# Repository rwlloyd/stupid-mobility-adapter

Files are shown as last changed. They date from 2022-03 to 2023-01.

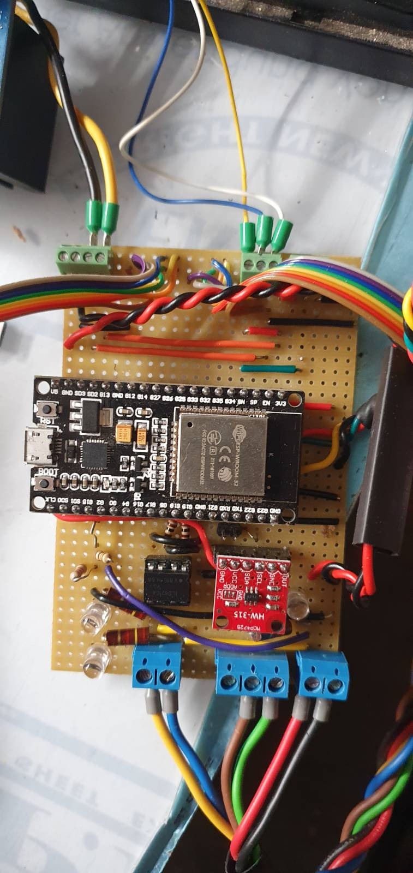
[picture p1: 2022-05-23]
signal-2022-04-29-131654.jpeg

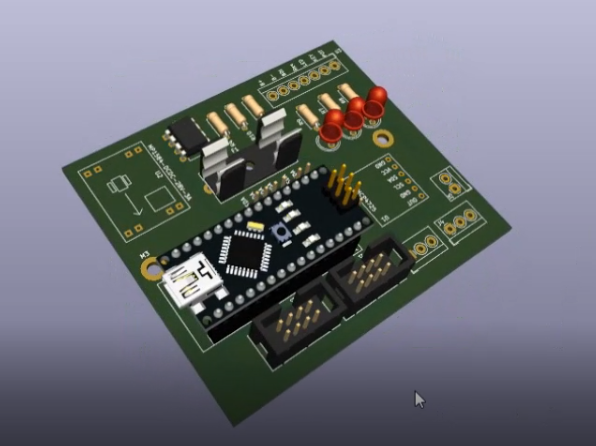
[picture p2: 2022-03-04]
stupid-mob-adap-v2-pcb-4-3-22.png

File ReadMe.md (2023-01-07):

# stupid-mobility-adapter

A repository for various microcontroller breakout boards that can be used to control mobile platforms (Modified Mobility Scooters).

## History of the stupid-mobility-adapter

During the COVID lockowns of 2020/21, it became necessary for me to have a Robotic platform that would work as a testing analogue to the one I didn't have access to at the time. This is how 'Scooterbot' was born. Initially intended as a personal, stipped back platform, liberated from the scrapheap, and built at minimal cost (<£250) the controller was fried and it had no steering column. These were replaced by an atmega 328 microcontroller and two BTS7960 half-bridge drivers. The PWM controlled drivers control the main DC drive motor and a steering motor. In this case, a 24V transaxle motor rated a 300-400W and a 24V linear actuator with feedback via a potentiometer (0-5V). Additionally, the drive motor has a 24V solenoid brake. 

After returning to work after lockdowns. A redesign of the platform I had been working on allowed me to use a modified version of the Scooterbot code to advance the project for work. This involved adding the ability to control a 'Curtis' style motor controller (Essentially three additional output signals. Enable, Direction and Speed (TTL, TTL, 0-5V)).

In addition to having a microcontroller to tell the motors, actuators etc. what to do. We also need to tell the microcontroller what to do. In previous projects, the communication with the microcontroller has been done over Serial connection with a simple communication protocol. With the microcontroller acting as a reciever, the sender was a companion computer (Raspberry Pi 3B+) reading inputs from a bluetooth games controller with custom python code. 

The addition of a companion computer adds a great deal of connectivity and processing power. Unfortunately, it also increases the complexity of the setup, and points of failure. Considering that basic control of the platform is a safety critical system, it is desirable to simplify the design. Additionally, as the prototypes of this project have performed on a variety of hardware, it is desirable to make this hardware intentionally generic, while keeping in mind its intended purpose.

The next version of the controller changed the microcontroller used to the ESP32. This allows us to cut out the companion computer for basic remote control using a bluetooth controller. There is also the addition of wifi, OTA updates using suitable sized compiled firmware and a large number of interface options. Overall simplification along the thinking of 'the best part is no part'. The drawback of this system is a reduction in CPU processing power.  

---

### stupid mobility adapter v2 

The culmination of the work on the ScooterBot and ARWAC v4 platforms. This board is intentionally generic. 
At the time of writing. It is not intended to fabricate this board. However, the PCB design is complete to the point of passing all Electrical Rules Checks

Important Hardware:

- Arduino Nano
- Adafruit MCP4725 12-bit DAC
- ILD615-2 Dual Optoisolator
- MP1584 DCDC Step Down (28V 3A)

Optional:

- 2 x BTS7960 Half-Bridge motor Drivers
- 2 x Electric Linear Actuator
- Mobility Scooter with Curtis style I/O

---

### stupid mobility adapter v3

As above, but ported to ESP32 with the addition of a Sony Dualshock3 Games contoller. Probably add some more bells and whistles too. 

Possibly:
- CAN Bus Tranciever
- encoder input
- Relays - Done!
- Status LEDS - Done on  the board. Headers for the panel?
- OLED for feedback/errors/messages - This may end up being done with a web interface

and that's just the hardware. Because we're using an esp32, we have the option for adding things like:

- Wifi
- A web interface/feedback
- ROS support (using micro-ROS)

## v3 PCB Problems

- The GND next to the VIN pin on the ESP32 Socket must be isolated
    - REASON: I misread the name when Making the footprint. It's actually CMD ( Something to do with the SPI Falsh chip. If you don't disconnect it, the ESP32 Can't Boot)
- LED 'D1' has the polarity reversed on the silkscreen.
- FB_0 has 5V and GND silkscreen swapped.
- 5V label on FB_0 and FB_1 should be 3V3
- The Board needs reverse polarity protection. Don't ask me how I know.
- A power LED on the 24V input would be useful.
- Should have broken out some power next to communicaton connections (Like I did with the relays)
- The Buzzer footprint needs to be correct. And connected to a pin capable of output :( 
- The Battery divider cannot be used while Wifi is enabled. Only discovered after install :(
    - Note: ADC2 pins cannot be used when Wi-Fi is used. So, if you’re using Wi-Fi and you’re having trouble getting the value from an ADC2 GPIO, you may consider using an ADC1 GPIO instead, that should solve your problem. from https://randomnerdtutorials.com/esp32-adc-analog-read-arduino-ide/

### Should have dones;
- A way to adjust the actuator endpoints on the board?
- A way to adjust the potential divider for the raw battery monitor. They're already talking about 48V!

However, we're running out of pins and It's probably time to embrace CAN bus, make the esp32 the 'master' node, then have nodes for the motor driver(s) ;), Actuators and any other custom bits. We should also start to be able to begin to use automotive devices....  

## Version 3.1 ideas

before I've even really finished the v3 hardware design, I've found things that I think it would be remiss of me to plan for. With 20/20 hindsight, some of these should have been included from the beginning.

### Servo PWM control From flight controllers

Control of the vehicle by more common means should be included. The first one that jumps to mind is the PWM contol that usually output by model radio recievers,
such as the ardupilot variety - that this hardware is eventually intendended to coexist alongside.

To implement this, we would need to 

- hand over control to the ardupilot system, taking commands from the autopilot in the form of throttle and steering inputs. 

- converting Servo signals to suitable outputs for the curtis unit / pwm driver / servo / hoverboardwheel / odrive combo that you need. 
https://www.benripley.com/diy/arduino/three-ways-to-read-a-pwm-signal-with-arduino/
https://lastminuteengineers.com/handling-esp32-gpio-interrupts-tutorial/

This would currently be controlled by the ps3 controller inputs, allowing the user to select different control methods while keeping the ablilty to contol the platform in case of emergencies or testing. 

### ESP acts as a radio control reciever 

### Servo Input to Flight Controllers

### Ros Input control

Here we are at a point where I need external input. HOw do people want to control all of this?

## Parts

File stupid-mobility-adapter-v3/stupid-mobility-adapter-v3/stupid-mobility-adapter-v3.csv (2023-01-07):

Source: | D:\dev\stupid-mobility-adapter\stupid-mobility-adapter-v3\stupid-mobility-adapter-v3\stupid-mobility-adapter-v3.kicad_sch
Date: | 05/12/2022 11:17:33
Tool: | Eeschema (6.0.2)
Generator: | C:\Program Files\KiCad\6.0\bin\scripting\plugins/bom_csv_grouped_by_value.py
Component Count: | 38
Individual Components:
Item | Qty | Reference(s) | Value | LibPart | Footprint | Datasheet | Field4
 |  | BZ1 | Buzzer | Device:Buzzer | stuipid-electronics-components:Buzzer_ABT-460-RC | ~
 |  | D1 | STAT | Device:LED | LED_THT:LED_D5.0mm | ~
 |  | D2 | REV | Device:LED | LED_THT:LED_D5.0mm | ~
 |  | D3 | KEY | Device:LED | LED_THT:LED_D5.0mm | ~
 |  | D4 | LED | Device:LED | LED_THT:LED_D5.0mm | ~
 |  | D5 | LED | Device:LED | LED_THT:LED_D5.0mm | ~
 |  | F1 | Fuse | Device:Fuse | Fuse:Fuse_Blade_ATO_directSolder | ~
 |  | J1 | BTS7968-0 | Connector_Generic:Conn_02x04_Odd_Even | Connector_IDC:IDC-Header_2x04_P2.54mm_Vertical | ~
 |  | J2 | Act0-FB | Connector_Generic:Conn_01x03 | TerminalBlock_4Ucon:TerminalBlock_4Ucon_1x03_P3.50mm_Horizontal | ~
 |  | J3 | BTS7968-1 | Connector_Generic:Conn_02x04_Odd_Even | Connector_IDC:IDC-Header_2x04_P2.54mm_Vertical | ~
 |  | J4 | Act1-FB | Connector_Generic:Conn_01x03 | TerminalBlock_4Ucon:TerminalBlock_4Ucon_1x03_P3.50mm_Horizontal | ~
 |  | J5 | ESTOP_INPUT | Connector_Generic:Conn_01x02 | TerminalBlock_4Ucon:TerminalBlock_4Ucon_1x02_P3.50mm_Horizontal | ~
 |  | J6 | UART | Connector_Generic:Conn_01x02 | Connector_PinHeader_2.54mm:PinHeader_1x02_P2.54mm_Vertical | ~
 |  | J7 | Relays | Connector_Generic:Conn_01x04 | Connector_PinHeader_2.54mm:PinHeader_1x04_P2.54mm_Vertical | ~
 |  | J8 | I2C | Connector_Generic:Conn_01x02 | Connector_PinHeader_2.54mm:PinHeader_1x02_P2.54mm_Vertical | ~
 |  | J9 | BATT_MON_SELECT | Connector_Generic:Conn_01x03 | Connector_PinHeader_2.54mm:PinHeader_1x03_P2.54mm_Vertical | ~
 |  | J10 | UART | Connector_Generic:Conn_01x02 | Connector_PinHeader_2.54mm:PinHeader_1x02_P2.54mm_Vertical | ~
 |  | Q1 | 2N3904 | Transistor_BJT:2N3904 | Package_TO_SOT_THT:TO-92_Inline | https://www.onsemi.com/pub/Collateral/2N3903-D.PDF
 |  | Q2 | 2N3904 | Transistor_BJT:2N3904 | Package_TO_SOT_THT:TO-92_Inline | https://www.onsemi.com/pub/Collateral/2N3903-D.PDF
 |  | R1 | R10K | Device:R | Resistor_THT:R_Axial_DIN0207_L6.3mm_D2.5mm_P7.62mm_Horizontal | ~
 |  | R2 | R1K5 | Device:R | Resistor_THT:R_Axial_DIN0207_L6.3mm_D2.5mm_P7.62mm_Horizontal | ~
 |  | R3 | R2K | Device:R | Resistor_THT:R_Axial_DIN0207_L6.3mm_D2.5mm_P7.62mm_Horizontal | ~
 |  | R4 | 100 | Device:R | Resistor_THT:R_Axial_DIN0207_L6.3mm_D2.5mm_P7.62mm_Horizontal | ~
 |  | R5 | R1K | Device:R | Resistor_THT:R_Axial_DIN0207_L6.3mm_D2.5mm_P7.62mm_Horizontal | ~
 |  | R6 | 100 | Device:R | Resistor_THT:R_Axial_DIN0207_L6.3mm_D2.5mm_P7.62mm_Horizontal | ~
 |  | R7 | 2k4 | Device:R | Resistor_THT:R_Axial_DIN0309_L9.0mm_D3.2mm_P12.70mm_Horizontal | ~
 |  | R8 | 2k4 | Device:R | Resistor_THT:R_Axial_DIN0309_L9.0mm_D3.2mm_P12.70mm_Horizontal | ~
 |  | R9 | 2k4 | Device:R | Resistor_THT:R_Axial_DIN0309_L9.0mm_D3.2mm_P12.70mm_Horizontal | ~
 |  | R10 | R1K | Device:R | Resistor_THT:R_Axial_DIN0207_L6.3mm_D2.5mm_P7.62mm_Horizontal | ~
 |  | R11 | R1K | Device:R | Resistor_THT:R_Axial_DIN0207_L6.3mm_D2.5mm_P7.62mm_Horizontal | ~
 |  | R12 | R1K | Device:R | Resistor_THT:R_Axial_DIN0207_L6.3mm_D2.5mm_P7.62mm_Horizontal | ~
 |  | R13 | R1K | Device:R | Resistor_THT:R_Axial_DIN0207_L6.3mm_D2.5mm_P7.62mm_Horizontal | ~
 |  | R14 | 100 | Device:R | Resistor_THT:R_Axial_DIN0207_L6.3mm_D2.5mm_P7.62mm_Horizontal | ~
 |  | U1 | MCP4725-Sparkfun | stupid-electronics-components-library:MCP4725-Sparkfun | stuipid-electronics-components:MPC4725-Sparkfun | https://www.sparkfun.com/products/12918
 |  | U2 | MP1584-DCDC-28V-3A | stupid-electronics-components-library:MP1584-DCDC-28V-3A | stuipid-electronics-components:MP1584 | https://www.monolithicpower.com/en/documentview/productdocument/index/version/2/document_type/Datasheet/lang/en/sku/MP1584EN-LF-Z/document_id/204
 |  | U3 | stupid-curtis-unit-basic | stupid-electronics-components-library:stupid-curtis-unit-basic | TerminalBlock_Phoenix:TerminalBlock_Phoenix_MKDS-3-7-5.08_1x07_P5.08mm_Horizontal
 |  | U4 | DUAL-OPTO | SparkFun-DiscreteSemi:DUAL-OPTOISOLATOR_SOIC8 | Package_DIP:DIP-8_W7.62mm | https://www.vishay.com/docs/83652/ild615.pdf | ILD615-2
 |  | U5 | ESP32DevKitV1 | stupid-electronics-components-library:ESP32DevKitV1 | stuipid-electronics-components:ESP32-DevKitV1
Collated Components:
Item | Qty | Reference(s) | Value | LibPart | Footprint | Datasheet | Field4
1 | 1 | BZ1 | Buzzer | Device:Buzzer | stuipid-electronics-components:Buzzer_ABT-460-RC | ~
2 | 1 | D1 | STAT | Device:LED | LED_THT:LED_D5.0mm | ~
3 | 1 | D2 | REV | Device:LED | LED_THT:LED_D5.0mm | ~
4 | 1 | D3 | KEY | Device:LED | LED_THT:LED_D5.0mm | ~
5 | 2 | D4, D5 | LED | Device:LED | LED_THT:LED_D5.0mm | ~
6 | 1 | F1 | Fuse | Device:Fuse | Fuse:Fuse_Blade_ATO_directSolder | ~
7 | 1 | J1 | BTS7968-0 | Connector_Generic:Conn_02x04_Odd_Even | Connector_IDC:IDC-Header_2x04_P2.54mm_Vertical | ~
8 | 1 | J2 | Act0-FB | Connector_Generic:Conn_01x03 | TerminalBlock_4Ucon:TerminalBlock_4Ucon_1x03_P3.50mm_Horizontal | ~
9 | 1 | J3 | BTS7968-1 | Connector_Generic:Conn_02x04_Odd_Even | Connector_IDC:IDC-Header_2x04_P2.54mm_Vertical | ~
10 | 1 | J4 | Act1-FB | Connector_Generic:Conn_01x03 | TerminalBlock_4Ucon:TerminalBlock_4Ucon_1x03_P3.50mm_Horizontal | ~
11 | 1 | J5 | ESTOP_INPUT | Connector_Generic:Conn_01x02 | TerminalBlock_4Ucon:TerminalBlock_4Ucon_1x02_P3.50mm_Horizontal | ~
12 | 2 | J6, J10 | UART | Connector_Generic:Conn_01x02 | Connector_PinHeader_2.54mm:PinHeader_1x02_P2.54mm_Vertical | ~
13 | 1 | J7 | Relays | Connector_Generic:Conn_01x04 | Connector_PinHeader_2.54mm:PinHeader_1x04_P2.54mm_Vertical | ~
14 | 1 | J8 | I2C | Connector_Generic:Conn_01x02 | Connector_PinHeader_2.54mm:PinHeader_1x02_P2.54mm_Vertical | ~
15 | 1 | J9 | BATT_MON_SELECT | Connector_Generic:Conn_01x03 | Connector_PinHeader_2.54mm:PinHeader_1x03_P2.54mm_Vertical | ~
16 | 2 | Q1, Q2 | 2N3904 | Transistor_BJT:2N3904 | Package_TO_SOT_THT:TO-92_Inline | https://www.onsemi.com/pub/Collateral/2N3903-D.PDF
17 | 1 | R1 | R10K | Device:R | Resistor_THT:R_Axial_DIN0207_L6.3mm_D2.5mm_P7.62mm_Horizontal | ~
18 | 1 | R2 | R1K5 | Device:R | Resistor_THT:R_Axial_DIN0207_L6.3mm_D2.5mm_P7.62mm_Horizontal | ~
19 | 1 | R3 | R2K | Device:R | Resistor_THT:R_Axial_DIN0207_L6.3mm_D2.5mm_P7.62mm_Horizontal | ~
20 | 3 | R4, R6, R14 | 100 | Device:R | Resistor_THT:R_Axial_DIN0207_L6.3mm_D2.5mm_P7.62mm_Horizontal | ~
21 | 5 | R5, R10, R11, R12, R13 | R1K | Device:R | Resistor_THT:R_Axial_DIN0207_L6.3mm_D2.5mm_P7.62mm_Horizontal | ~
22 | 3 | R7, R8, R9 | 2k4 | Device:R | Resistor_THT:R_Axial_DIN0309_L9.0mm_D3.2mm_P12.70mm_Horizontal | ~
23 | 1 | U1 | MCP4725-Sparkfun | stupid-electronics-components-library:MCP4725-Sparkfun | stuipid-electronics-components:MPC4725-Sparkfun | https://www.sparkfun.com/products/12918
24 | 1 | U2 | MP1584-DCDC-28V-3A | stupid-electronics-components-library:MP1584-DCDC-28V-3A | stuipid-electronics-components:MP1584 | https://www.monolithicpower.com/en/documentview/productdocument/index/version/2/document_type/Datasheet/lang/en/sku/MP1584EN-LF-Z/document_id/204
25 | 1 | U3 | stupid-curtis-unit-basic | stupid-electronics-components-library:stupid-curtis-unit-basic | TerminalBlock_Phoenix:TerminalBlock_Phoenix_MKDS-3-7-5.08_1x07_P5.08mm_Horizontal
26 | 1 | U4 | DUAL-OPTO | SparkFun-DiscreteSemi:DUAL-OPTOISOLATOR_SOIC8 | Package_DIP:DIP-8_W7.62mm | https://www.vishay.com/docs/83652/ild615.pdf | ILD615-2
27 | 1 | U5 | ESP32DevKitV1 | stupid-electronics-components-library:ESP32DevKitV1 | stuipid-electronics-components:ESP32-DevKitV1

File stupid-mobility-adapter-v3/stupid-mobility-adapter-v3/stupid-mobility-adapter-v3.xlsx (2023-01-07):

Source: | D:\dev\stupid-mobility-adapter\stupid-mobility-adapter-v3\stupid-mobility-adapter-v3\stupid-mobility-adapter-v3.kicad_sch
Date: | 2022-11-21T21:58:15.99999999627470925
Tool: | Eeschema (6.0.0)
Generator: | C:\Program Files\KiCad\6.0\bin\scripting\plugins/bom_csv_grouped_by_value_with_fp.py
Component Count: | 38
Ref | Qnty | Value | Cmp name | Footprint | Description | Vendor
BZ1, | 1 | Buzzer | Buzzer | stuipid-electronics-components:Buzzer_ABT-460-RC | Buzzer, polarized
D1, | 1 | STAT | LED | LED_THT:LED_D5.0mm | Light emitting diode
D2, | 1 | REV | LED | LED_THT:LED_D5.0mm | Light emitting diode
D3, | 1 | KEY | LED | LED_THT:LED_D5.0mm | Light emitting diode
D4, D5, | 2 | LED | LED | LED_THT:LED_D5.0mm | Light emitting diode
F1, | 1 | Fuse | Fuse | Fuse:Fuse_Blade_ATO_directSolder | Fuse
J1, | 1 | BTS7968-0 | Conn_02x04_Odd_Even | Connector_IDC:IDC-Header_2x04_P2.54mm_Vertical | Generic connector, double row, 02x04, odd/even pin numbering scheme (row 1 odd numbers, row 2 even numbers), script generated (kicad-library-utils/schlib/autogen/connector/)
J2, | 1 | Act0-FB | Conn_01x03 | TerminalBlock_4Ucon:TerminalBlock_4Ucon_1x03_P3.50mm_Horizontal | Generic connector, single row, 01x03, script generated (kicad-library-utils/schlib/autogen/connector/)
J3, | 1 | BTS7968-1 | Conn_02x04_Odd_Even | Connector_IDC:IDC-Header_2x04_P2.54mm_Vertical | Generic connector, double row, 02x04, odd/even pin numbering scheme (row 1 odd numbers, row 2 even numbers), script generated (kicad-library-utils/schlib/autogen/connector/)
J4, | 1 | Act1-FB | Conn_01x03 | TerminalBlock_4Ucon:TerminalBlock_4Ucon_1x03_P3.50mm_Horizontal | Generic connector, single row, 01x03, script generated (kicad-library-utils/schlib/autogen/connector/)
J5, | 1 | ESTOP_INPUT | Conn_01x02 | TerminalBlock_4Ucon:TerminalBlock_4Ucon_1x02_P3.50mm_Horizontal | Generic connector, single row, 01x02, script generated (kicad-library-utils/schlib/autogen/connector/)
J6, J10, | 2 | UART | Conn_01x02 | Connector_PinHeader_2.54mm:PinHeader_1x02_P2.54mm_Vertical | Generic connector, single row, 01x02, script generated (kicad-library-utils/schlib/autogen/connector/)
J7, | 1 | Relays | Conn_01x04 | Connector_PinHeader_2.54mm:PinHeader_1x04_P2.54mm_Vertical | Generic connector, single row, 01x04, script generated (kicad-library-utils/schlib/autogen/connector/)
J8, | 1 | I2C | Conn_01x02 | Connector_PinHeader_2.54mm:PinHeader_1x02_P2.54mm_Vertical | Generic connector, single row, 01x02, script generated (kicad-library-utils/schlib/autogen/connector/)
J9, | 1 | BATT_MON_SELECT | Conn_01x03 | Connector_PinHeader_2.54mm:PinHeader_1x03_P2.54mm_Vertical | Generic connector, single row, 01x03, script generated (kicad-library-utils/schlib/autogen/connector/)
Q1, Q2, | 2 | 2N3904 | 2N3904 | Package_TO_SOT_THT:TO-92_Inline | 0.2A Ic, 40V Vce, Small Signal NPN Transistor, TO-92
R1, | 1 | R10K | R | Resistor_THT:R_Axial_DIN0207_L6.3mm_D2.5mm_P7.62mm_Horizontal | Resistor
R2, | 1 | R1K5 | R | Resistor_THT:R_Axial_DIN0207_L6.3mm_D2.5mm_P7.62mm_Horizontal | Resistor
R3, | 1 | R2K | R | Resistor_THT:R_Axial_DIN0207_L6.3mm_D2.5mm_P7.62mm_Horizontal | Resistor
R4, R6, R14, | 3 | 100 | R | Resistor_THT:R_Axial_DIN0207_L6.3mm_D2.5mm_P7.62mm_Horizontal | Resistor
R5, R10, R11, R12, R13, | 5 | R1K | R | Resistor_THT:R_Axial_DIN0207_L6.3mm_D2.5mm_P7.62mm_Horizontal | Resistor
R7, R8, R9, | 3 | 2k4 | R | Resistor_THT:R_Axial_DIN0309_L9.0mm_D3.2mm_P12.70mm_Horizontal | Resistor
U1, | 1 | MCP4725-Sparkfun | MCP4725-Sparkfun | stuipid-electronics-components:MPC4725-Sparkfun | Sparkfun 12-bit DAC- I2C
U2, | 1 | MP1584-DCDC-28V-3A | MP1584-DCDC-28V-3A | stuipid-electronics-components:MP1584
U3, | 1 | stupid-curtis-unit-basic | stupid-curtis-unit-basic | TerminalBlock_Phoenix:TerminalBlock_Phoenix_MKDS-3-7-5.08_1x07_P5.08mm_Horizontal
U4, | 1 | DUAL-OPTO | DUAL-OPTOISOLATOR_SOIC8 | Package_DIP:DIP-8_W7.62mm
U5, | 1 | ESP32DevKitV1 | ESP32DevKitV1 | stuipid-electronics-components:ESP32-DevKitV1 | kicad6.0 symbol for ESP32DevKitV1 Board

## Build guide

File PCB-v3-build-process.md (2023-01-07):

# Mobility Adapter PCB (v3) firmware configuration procedure

This configuration process guides you through preparing hardware and configuring firmware for the Mobility-Adapter-v3 PCB as of late 2022.  

## Cut redundant traces on PCB (v3).

The pin next to VIN on the ESP32 Module footprint, Labelled GND, is a mistake. The pis should not be connected to ground. 
1. Cut the traces for that pin, connecting it to the ground plane.

2. Check that the pin is isolated using a multimeter between the isolated pin and any other GND point.

## Adjust the Buck Converter Voltage

Once the main motor driver header, fuse and buck module are soldered, the output of the buck can be set to 5v.

1. Connect the 12-30v supply voltage to the B+ and B-. NOTE. This board doesn't have reverse polarity protection. DOUBLE CHECK POLARITY.

2. Power up the board and adjust the trim pot on the buck converter to 5.0 - 5.1V. The 5V and GNC pins associated with the relays header are convenient test points.

## Setup Bluetooth Controller 

1. Flash the Ps3Address.ino file to the ESP32. it can be found at;

`firmware\PS3Controller\Ps3Address\Ps3Address.ino`

2. install and run the 'SixAxisPairTool' and enter the MAC address discovered in the previous step.

3. test the pairing using the Ps3Test-Friendly.ino sketch, found at;

`firmware\PS3Controller\Ps3Test-Friendly\Ps3Test-Friendly.ino`

It's necessary to modify the folloing line in the setup function, substituting in the correct mac address for this particular pairing.

`Ps3.begin("xx:xx:xx:xx:xx:xx");`

## Configure Firmware for Specific Platform

While Each platform will need a custom configuration regarding the use of the output, all platforms will require the following modifications.

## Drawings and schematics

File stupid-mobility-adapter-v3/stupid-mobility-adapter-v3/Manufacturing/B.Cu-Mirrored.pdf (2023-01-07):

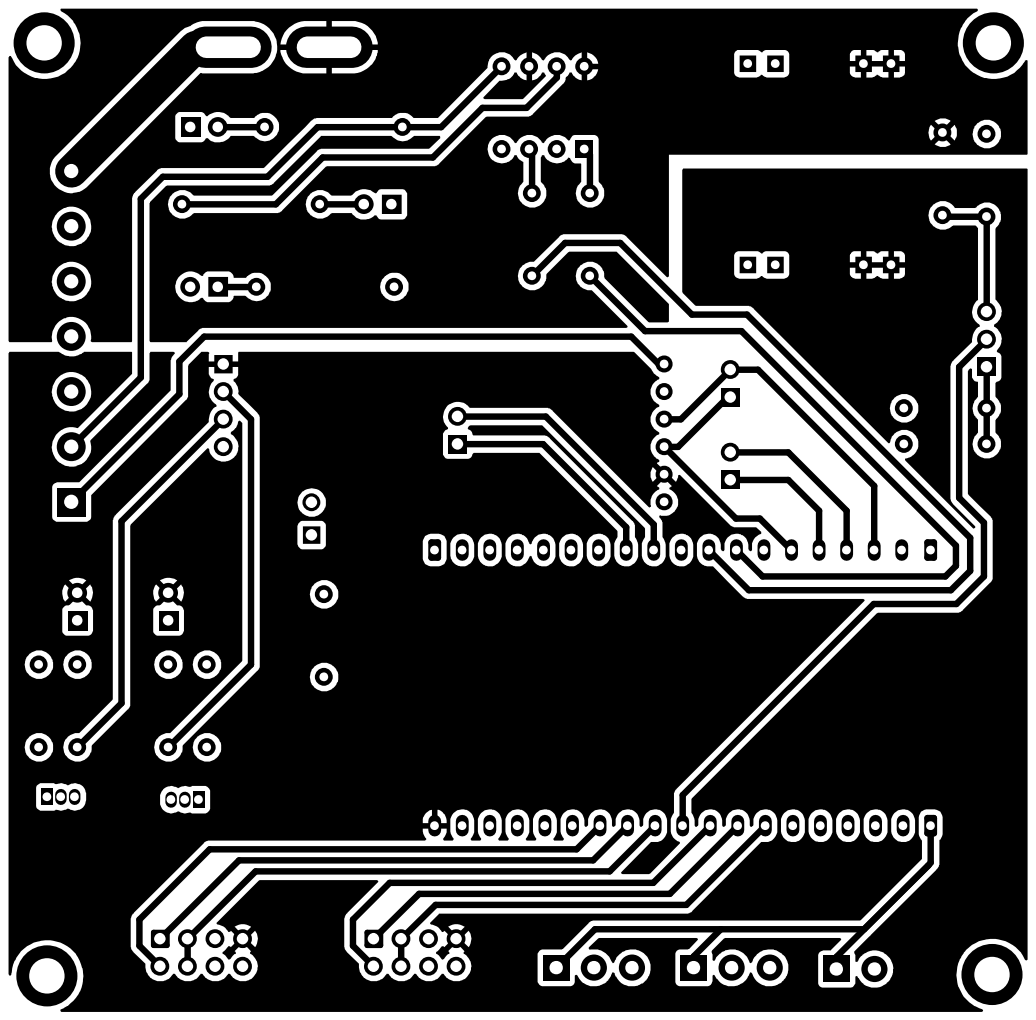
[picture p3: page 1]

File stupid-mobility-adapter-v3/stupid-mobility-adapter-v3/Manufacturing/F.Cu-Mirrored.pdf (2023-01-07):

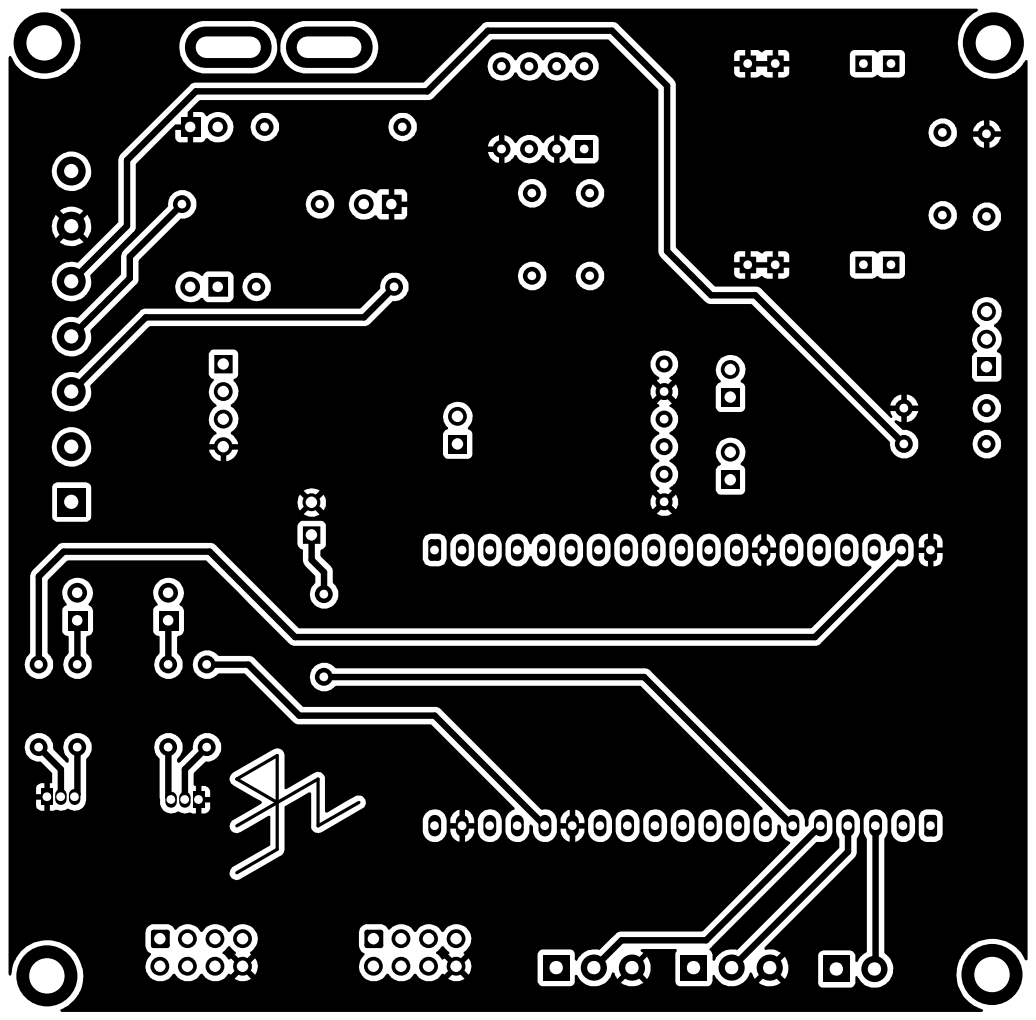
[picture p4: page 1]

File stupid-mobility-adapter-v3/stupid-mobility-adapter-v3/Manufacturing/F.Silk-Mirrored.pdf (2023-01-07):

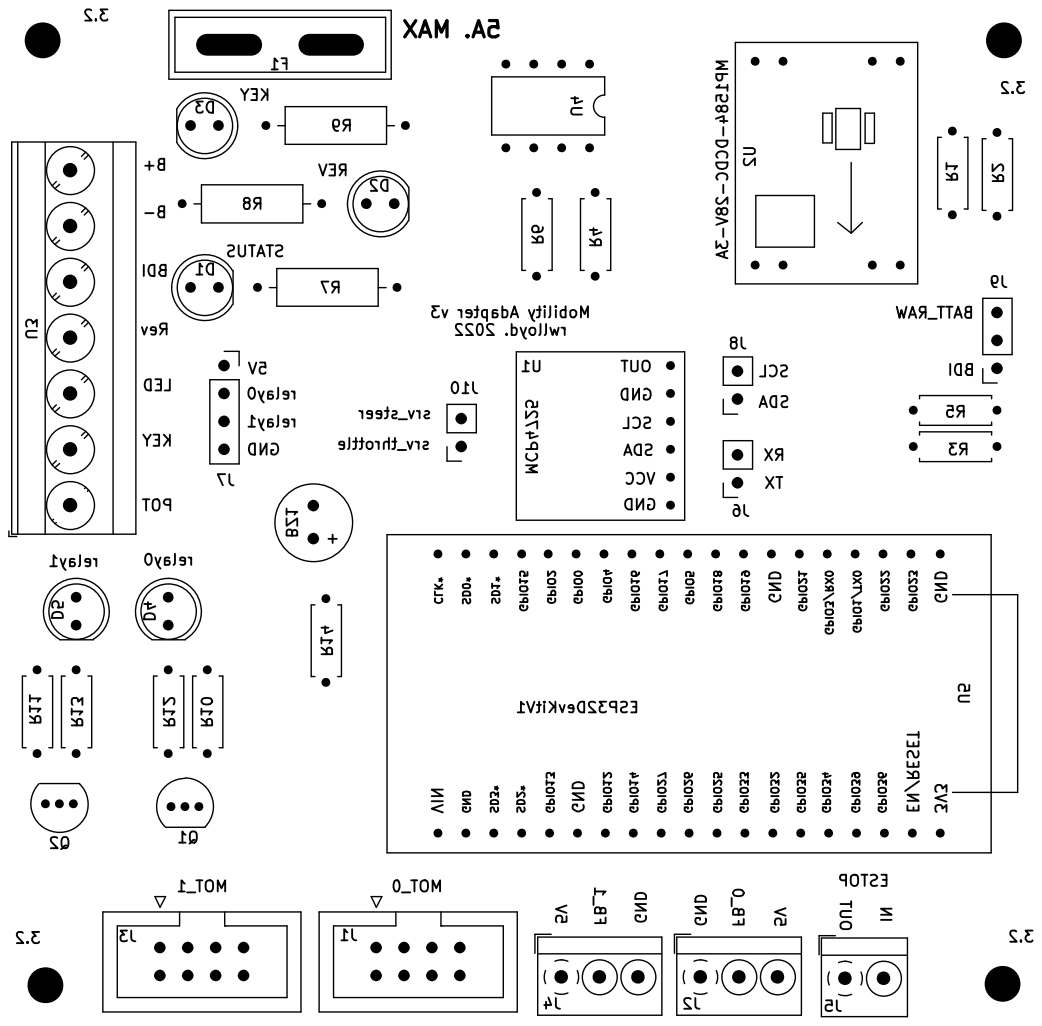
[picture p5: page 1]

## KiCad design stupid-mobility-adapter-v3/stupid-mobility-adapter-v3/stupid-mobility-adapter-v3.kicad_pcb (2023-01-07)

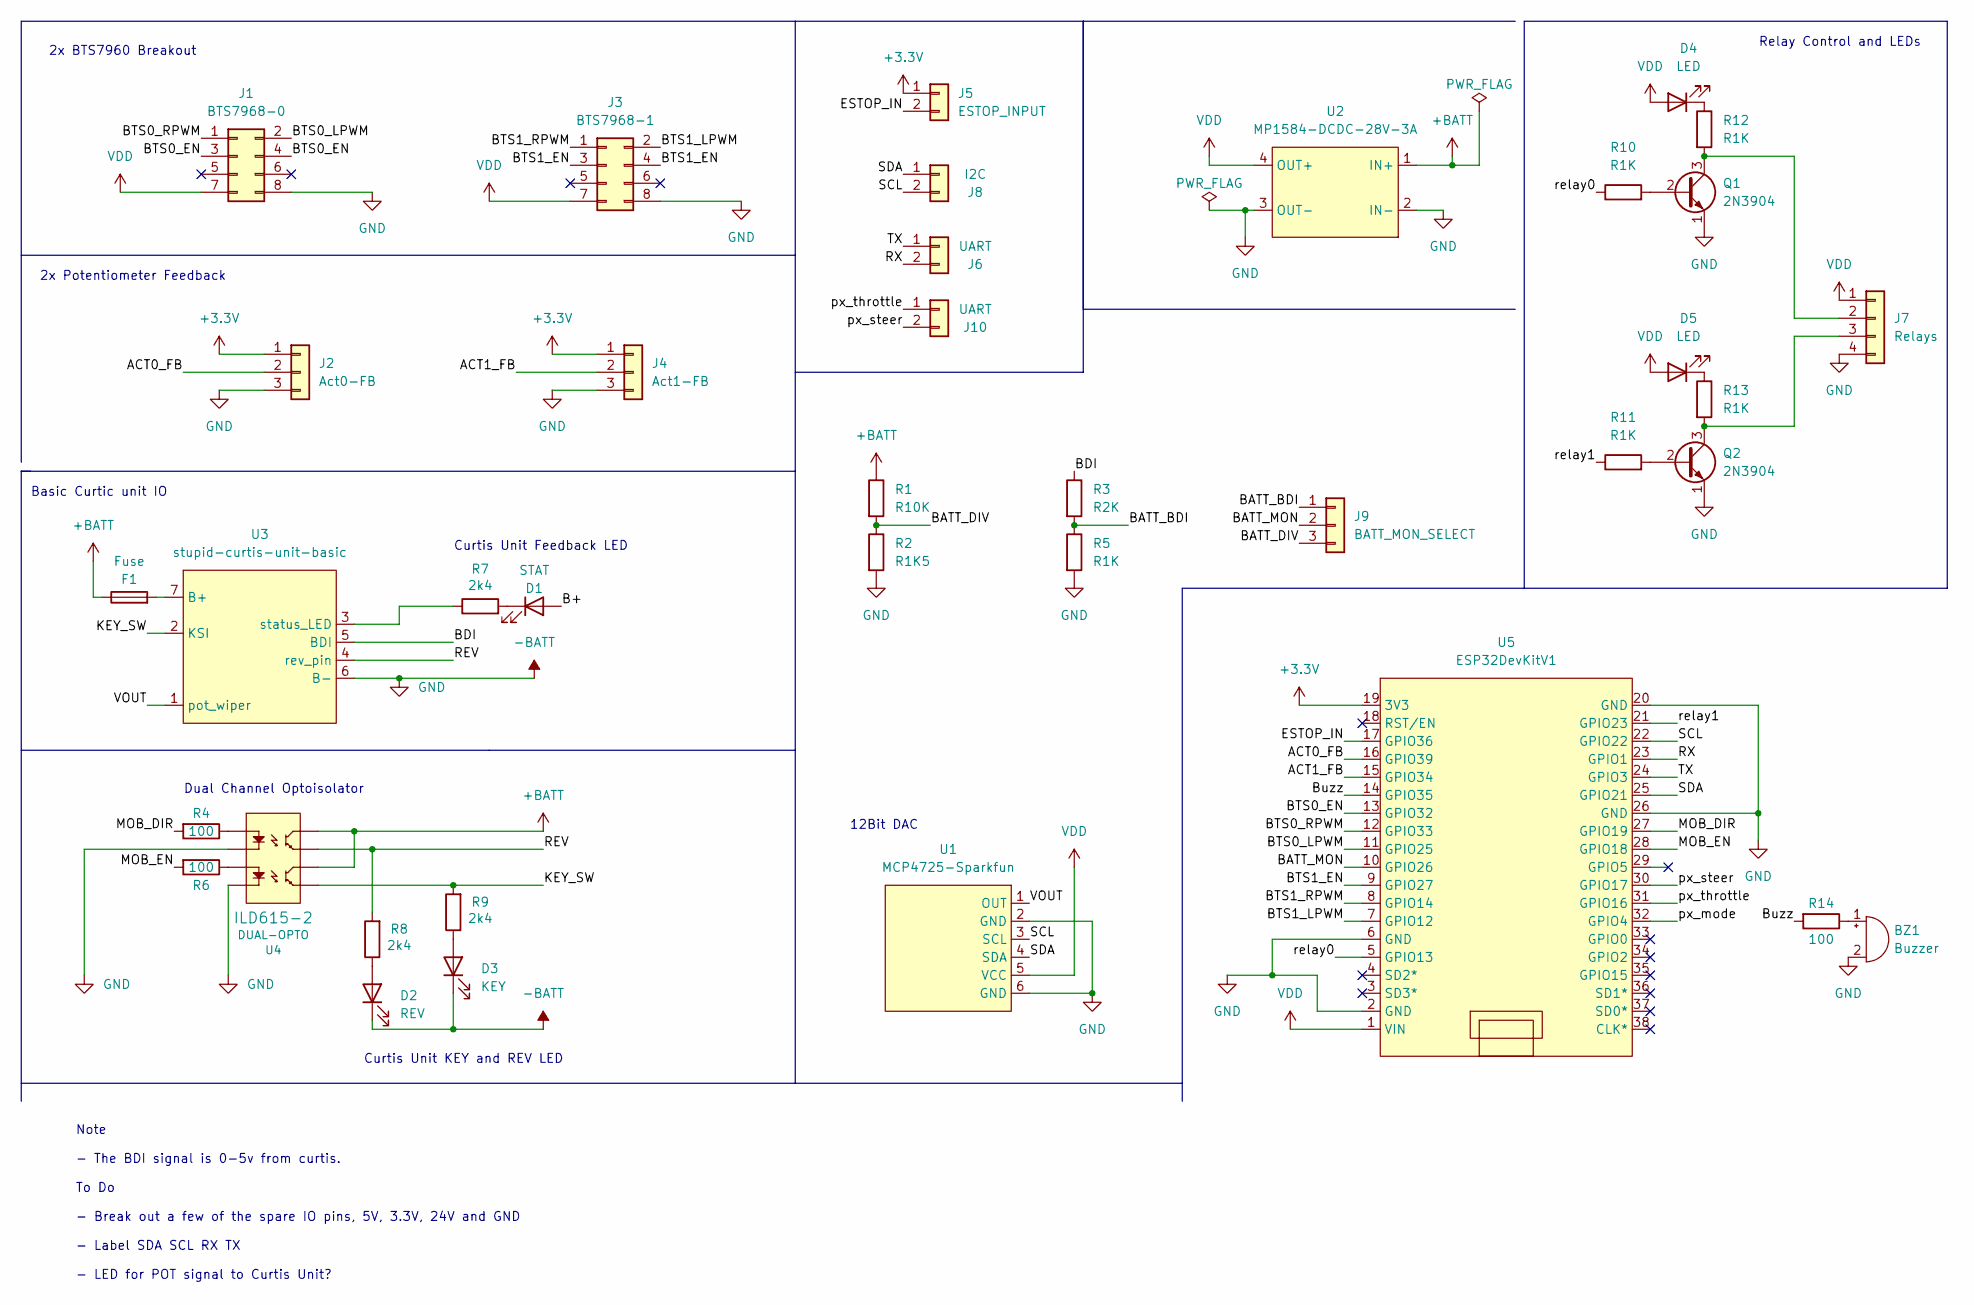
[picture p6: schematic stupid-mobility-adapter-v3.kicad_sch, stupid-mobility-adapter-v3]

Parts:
BZ1: Buzzer; Buzzer_ABT-460-RC
D1: STAT; LED_D5.0mm
D2: REV; LED_D5.0mm
D3: KEY; LED_D5.0mm
D4, D5: LED; LED_D5.0mm
F1: Fuse; Fuse_Blade_ATO_directSolder
J1: BTS7968-0; IDC-Header_2x04_P2.54mm_Vertical
J2: Act0-FB; TerminalBlock_4Ucon_1x03_P3.50mm_Horizontal
J3: BTS7968-1; IDC-Header_2x04_P2.54mm_Vertical
J4: Act1-FB; TerminalBlock_4Ucon_1x03_P3.50mm_Horizontal
J5: ESTOP_INPUT; TerminalBlock_4Ucon_1x02_P3.50mm_Horizontal
J6, J10: UART; PinHeader_1x02_P2.54mm_Vertical
J7: Relays; PinHeader_1x04_P2.54mm_Vertical
J8: I2C; PinHeader_1x02_P2.54mm_Vertical
J9: BATT_MON_SELECT; PinHeader_1x03_P2.54mm_Vertical
Q1, Q2: 2N3904; TO-92_Inline
R1: R10K; R_Axial_DIN0207_L6.3mm_D2.5mm_P7.62mm_Horizontal
R2: R1K5; R_Axial_DIN0207_L6.3mm_D2.5mm_P7.62mm_Horizontal
R3: R2K; R_Axial_DIN0207_L6.3mm_D2.5mm_P7.62mm_Horizontal
R4, R6, R14: 100; R_Axial_DIN0207_L6.3mm_D2.5mm_P7.62mm_Horizontal
R5, R10, R11, R12, R13: R1K; R_Axial_DIN0207_L6.3mm_D2.5mm_P7.62mm_Horizontal
R7, R8, R9: 2k4; R_Axial_DIN0309_L9.0mm_D3.2mm_P12.70mm_Horizontal
U1: MCP4725-Sparkfun; MPC4725-Sparkfun
U2: MP1584-DCDC-28V-3A; MP1584
U3: stupid-curtis-unit-basic; TerminalBlock_Phoenix_MKDS-3-7-5.08_1x07_P5.08mm_Horizontal
U4: DUAL-OPTO; DIP-8_W7.62mm
U5: ESP32DevKitV1; ESP32-DevKitV1

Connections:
+3V3: J2.1, J4.1, J5.1, U5.19 (3V3)
+BATT: F1.1, R1.1, U2.1 (IN+), U4.6 (CL2), U4.8 (CL1)
-BATT: BZ1.2 (+), D2.1 (K), D3.1 (K), J1.8, J2.3, J3.8, J4.3, J7.4, Q1.1 (E), Q2.1 (E), R2.2, R5.2, U1.2 (GND), U1.6 (GND), U2.2 (IN-), U2.3 (OUT-), U3.6 (B-), U4.2 (C1), U4.4 (C2), U5.2 (GND), U5.6 (GND), U5.20 (GND), U5.26 (GND)
/ACT0_FB: J2.2, U5.16 (GPIO39)
/ACT1_FB: J4.2, U5.15 (GPIO34)
/B+: D1.2 (A)
/BATT_BDI: J9.1, R3.2, R5.1
/BATT_DIV: J9.3, R1.2, R2.1
/BATT_MON: J9.2, U5.10 (GPIO26)
/BDI: R3.1, U3.5 (BDI)
/BTS0_EN: J1.3, J1.4, U5.13 (GPIO32)
/BTS0_LPWM: J1.2, U5.11 (GPIO25)
/BTS0_RPWM: J1.1, U5.12 (GPIO33)
/BTS1_EN: J3.3, J3.4, U5.9 (GPIO27)
/BTS1_LPWM: J3.2, U5.7 (GPIO12)
/BTS1_RPWM: J3.1, U5.8 (GPIO14)
/Buzz: R14.2, U5.14 (GPIO35)
/ESTOP_IN: J5.2, U5.17 (GPIO36)
/KEY_SW: R9.2, U3.2 (KSI), U4.5 (EM2)
/MOB_DIR: R4.2, U5.27 (GPIO19)
/MOB_EN: R6.2, U5.28 (GPIO18)
/REV: R8.2, U3.4 (rev_pin), U4.7 (EM1)
/RX: J6.2, U5.23 (GPIO1)
/SCL: J8.2, U1.3 (SCL), U5.22 (GPIO22)
/SDA: J8.1, U1.4 (SDA), U5.25 (GPIO21)
/TX: J6.1, U5.24 (GPIO3)
/VOUT: U1.1 (OUT), U3.1 (pot_wiper)
/px_mode: U5.32 (GPIO4)
/px_steer: J10.2, U5.30 (GPIO17)
/px_throttle: J10.1, U5.31 (GPIO16)
/relay0: R10.1, U5.5 (GPIO13)
/relay1: R11.1, U5.21 (GPIO23)
unnamed: BZ1.1 (-), R14.1
unnamed: D1.1 (K), R7.2
unnamed: D2.2 (A), R8.1
unnamed: D3.2 (A), R9.1
unnamed: D4.1 (K), R12.1
unnamed: D5.1 (K), R13.1
unnamed: F1.2, U3.7 (B+)
unnamed: J7.2, Q1.3 (C), R12.2
unnamed: J7.3, Q2.3 (C), R13.2
unnamed: Q1.2 (B), R10.2
unnamed: Q2.2 (B), R11.2
unnamed: R4.1, U4.1 (A1)
unnamed: R6.1, U4.3 (A2)
unnamed: R7.1, U3.3 (status_LED)
VDD: D4.2 (A), D5.2 (A), J1.7, J3.7, J7.1, U1.5 (VCC), U2.4 (OUT+), U5.1 (VIN)

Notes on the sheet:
2x BTS7960 Breakout
Basic Curtic unit IO
Curtis Unit KEY and REV LED
Dual Channel Optoisolator
12Bit DAC
Curtis Unit Feedback LED
Note - The BDI signal is 0-5v from curtis. To Do - Break out a few of the spare IO pins, 5V, 3.3V, 24V and GND - Label SDA SCL RX TX - LED for POT signal to Curtis Unit?
Relay Control and LEDs
2x Potentiometer Feedback

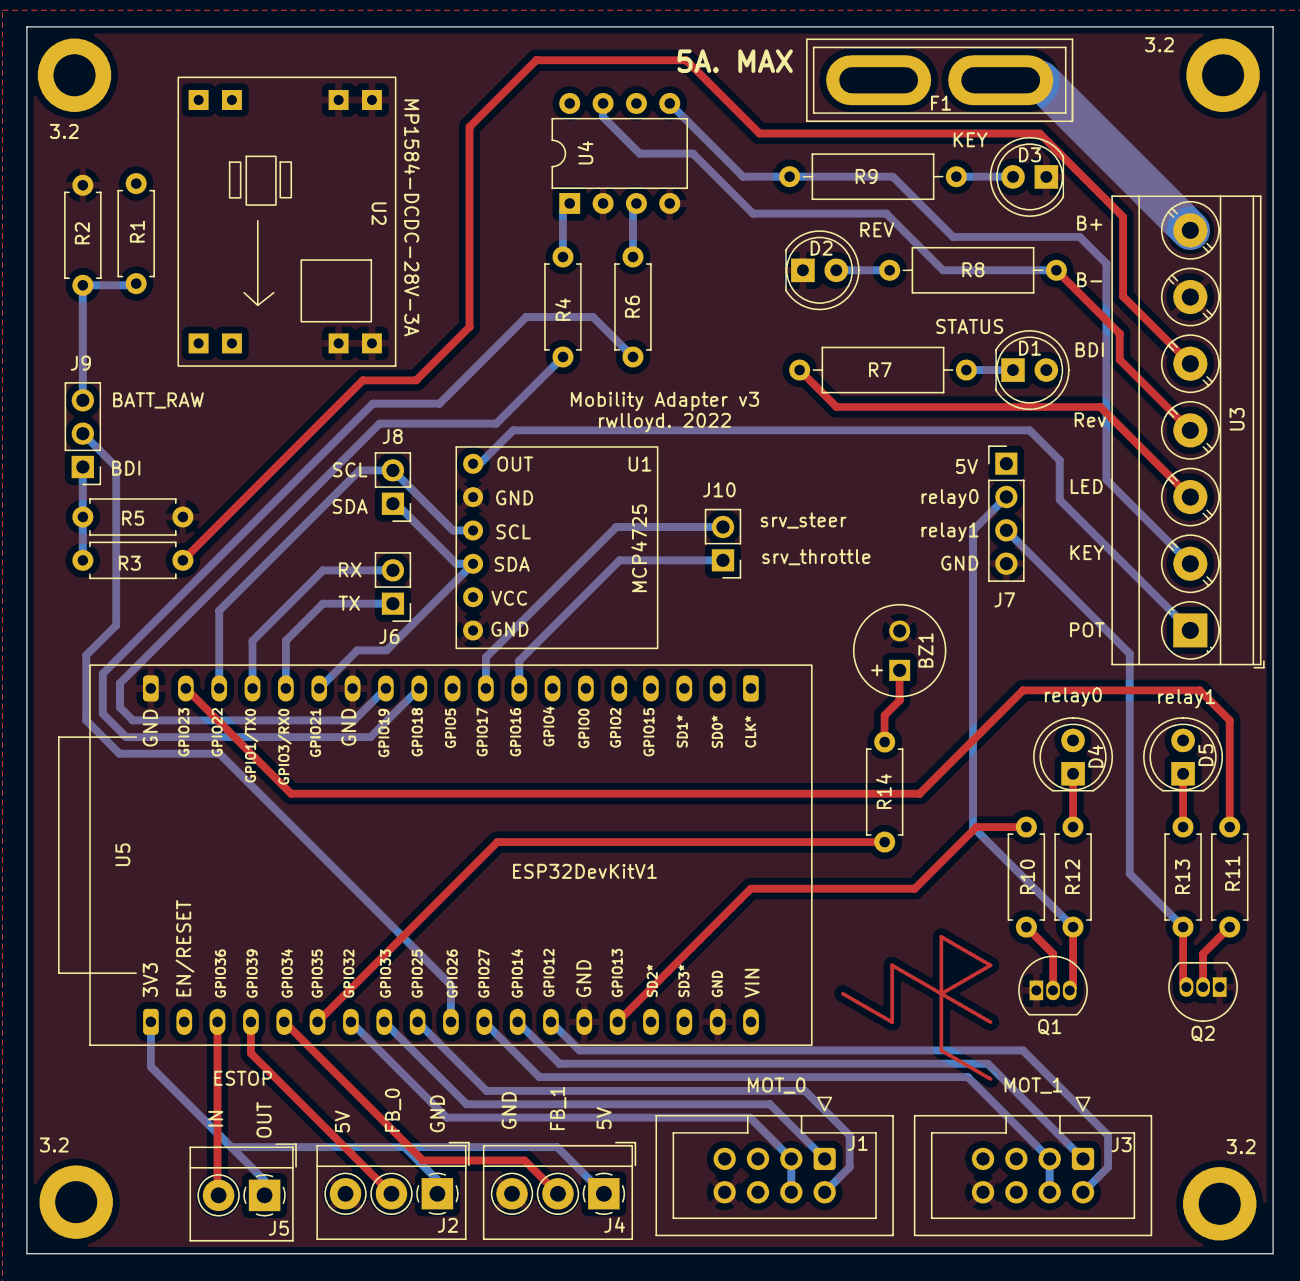
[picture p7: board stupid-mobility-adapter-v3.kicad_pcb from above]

Board: 2 copper layers, 94.9 x 93.5 mm, 42 parts (0 on the bottom side), 45 nets.

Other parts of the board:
3.2, 3.2#2, 3.2#3, 3.2#4: MountingHole_3.2mm_M3_DIN965_Pad

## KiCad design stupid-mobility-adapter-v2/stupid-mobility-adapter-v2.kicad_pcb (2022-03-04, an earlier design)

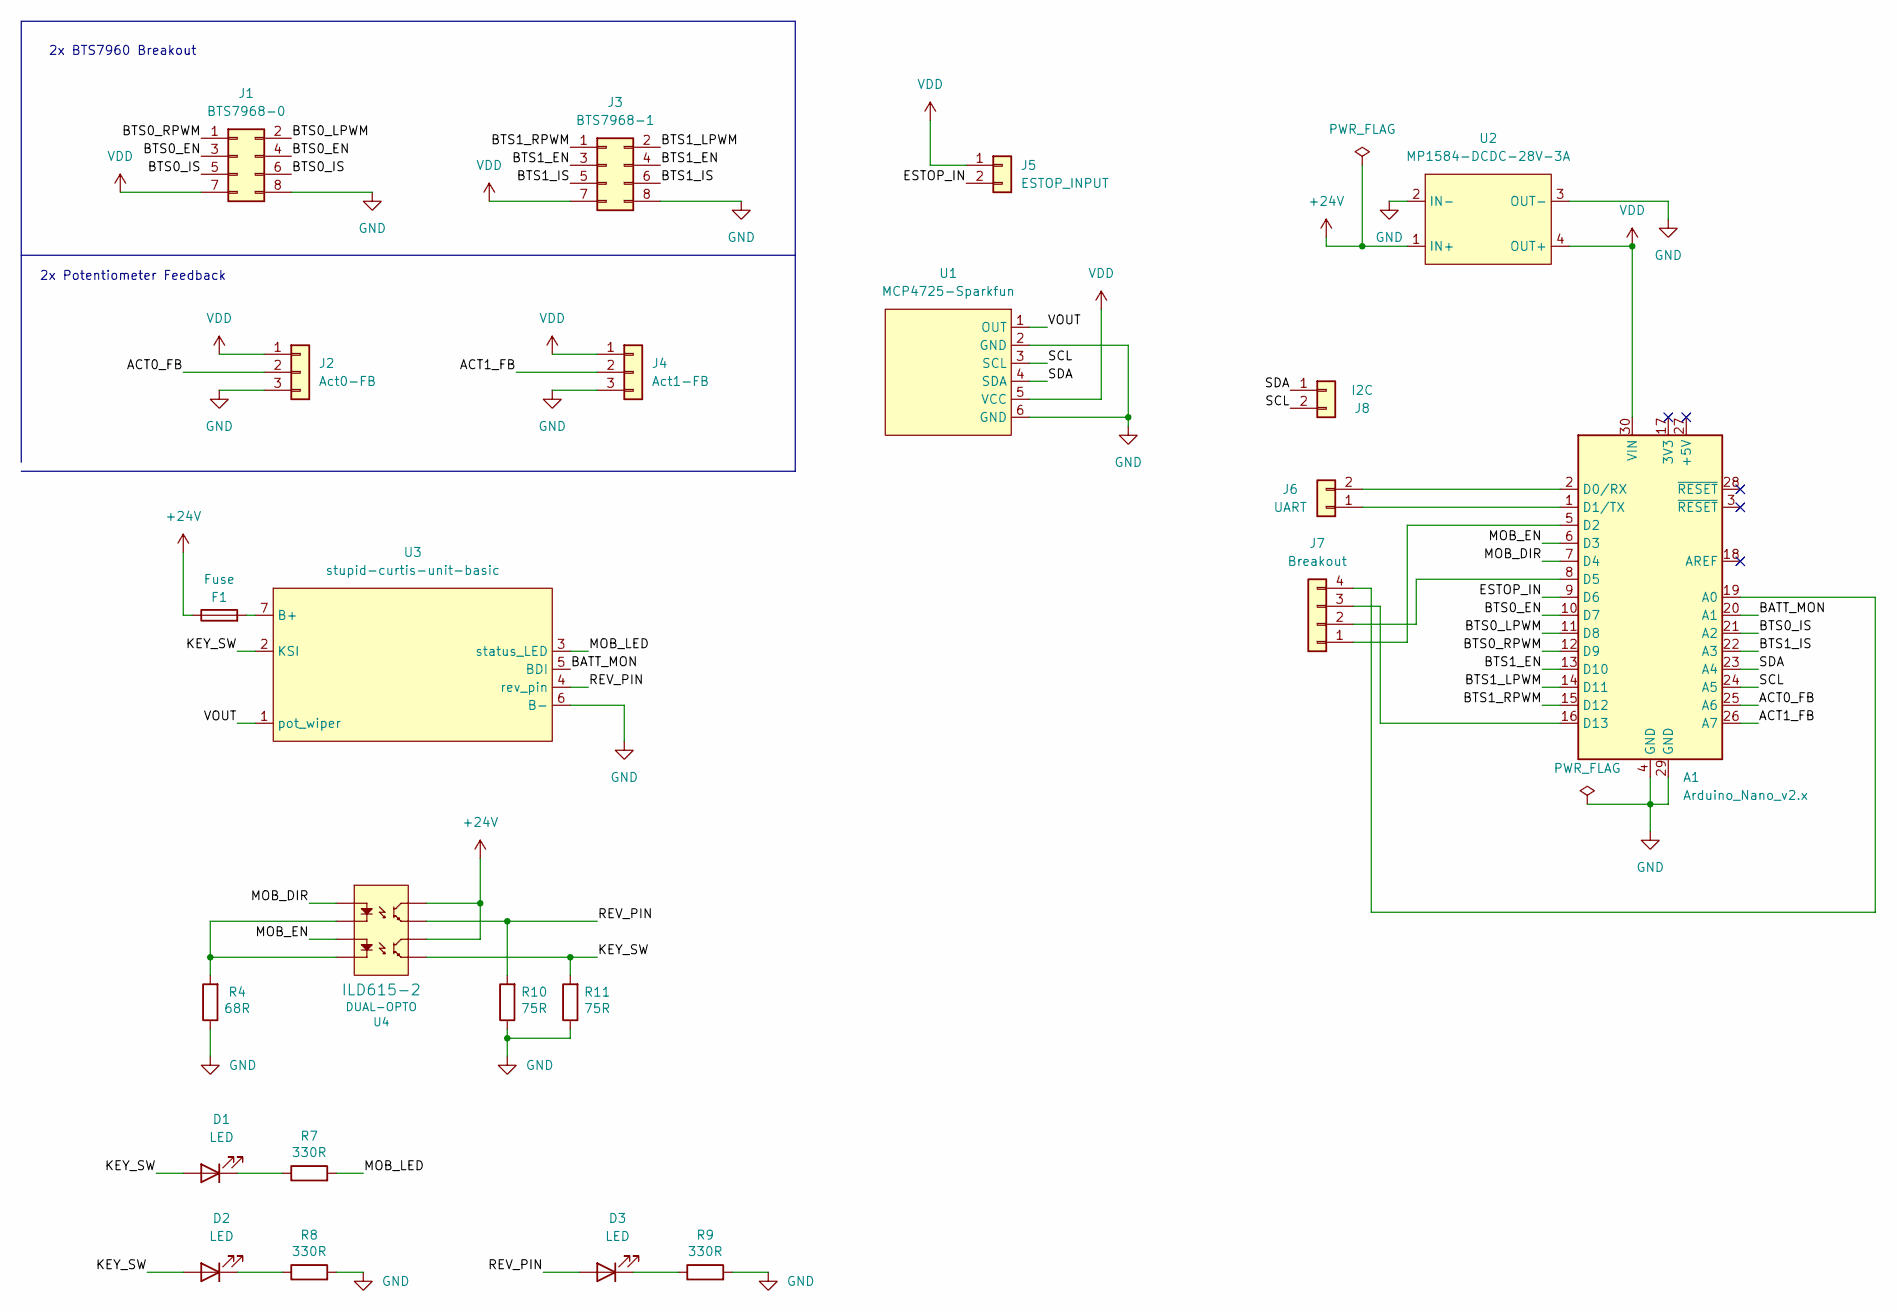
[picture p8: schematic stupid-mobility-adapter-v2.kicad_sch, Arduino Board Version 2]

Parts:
A1: Arduino_Nano_v2.x; Arduino_Nano
D1, D2, D3: LED; LED_D5.0mm
F1: Fuse; Fuseholder_Cylinder-5x20mm_Schurter_0031_8201_Horizontal_Op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
J1: BTS7968-0; IDC-Header_2x04_P2.54mm_Vertical
J2: Act0-FB; TerminalBlock_4Ucon_1x03_P3.50mm_Horizontal
J3: BTS7968-1; IDC-Header_2x04_P2.54mm_Vertical
J4: Act1-FB; TerminalBlock_4Ucon_1x03_P3.50mm_Horizontal
J5: ESTOP_INPUT; TerminalBlock_4Ucon_1x02_P3.50mm_Horizontal
J6: UART; PinHeader_1x02_P2.54mm_Vertical
J7: Breakout; PinHeader_1x04_P2.54mm_Vertical
J8: I2C; PinHeader_1x02_P2.54mm_Vertical
R4: 68R; R_Axial_DIN0207_L6.3mm_D2.5mm_P7.62mm_Horizontal
R7, R8, R9: 330R; R_Axial_DIN0207_L6.3mm_D2.5mm_P7.62mm_Horizontal
R10, R11: 75R; R_Axial_DIN0207_L6.3mm_D2.5mm_P7.62mm_Horizontal
U1: MCP4725-Sparkfun; MPC4725-Sparkfun
U2: MP1584-DCDC-28V-3A; MP1584
U3: stupid-curtis-unit-basic; TerminalBlock_4Ucon_1x07_P3.50mm_Horizontal
U4: DUAL-OPTO; DIP-8_W7.62mm

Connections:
+24V: F1.1, U2.1 (IN+), U4.6 (CL2), U4.8 (CL1)
/ACT0_FB: A1.25 (A6), J2.2
/ACT1_FB: A1.26 (A7), J4.2
/BATT_MON: A1.20 (A1), U3.5 (BDI)
/BTS0_EN: A1.10 (D7), J1.3, J1.4
/BTS0_IS: A1.21 (A2), J1.5, J1.6
/BTS0_LPWM: A1.11 (D8), J1.2
/BTS0_RPWM: A1.12 (D9), J1.1
/BTS1_EN: A1.13 (D10), J3.3, J3.4
/BTS1_IS: A1.22 (A3), J3.5, J3.6
/BTS1_LPWM: A1.14 (D11), J3.2
/BTS1_RPWM: A1.15 (D12), J3.1
/ESTOP_IN: A1.9 (D6), J5.2
/KEY_SW: D1.2 (A), D2.2 (A), R11.2, U3.2 (KSI), U4.5 (EM2)
/MOB_DIR: A1.7 (D4), U4.1 (A1)
/MOB_EN: A1.6 (D3), U4.3 (A2)
/MOB_LED: R7.2, U3.3 (status_LED)
/REV_PIN: D3.2 (A), R10.2, U3.4 (rev_pin), U4.7 (EM1)
/SCL: A1.24 (A5), J8.2, U1.3 (SCL)
/SDA: A1.23 (A4), J8.1, U1.4 (SDA)
/VOUT: U1.1 (OUT), U3.1 (pot_wiper)
GND: A1.4 (GND), A1.29 (GND), J1.8, J2.3, J3.8, J4.3, R4.1, R8.2, R9.2, R10.1, R11.1, U1.2 (GND), U1.6 (GND), U2.2 (IN-), U2.3 (OUT-), U3.6 (B-)
unnamed: A1.1 (D1/TX), J6.1
unnamed: A1.2 (D0/RX), J6.2
unnamed: A1.5 (D2), J7.1
unnamed: A1.8 (D5), J7.2
unnamed: A1.19 (A0), J7.4
unnamed: D1.1 (K), R7.1
unnamed: D2.1 (K), R8.1
unnamed: D3.1 (K), R9.1
unnamed: F1.2, U3.7 (B+)
unnamed: A1.16 (D13), J7.3
unnamed: R4.2, U4.2 (C1), U4.4 (C2)
VDD: A1.30 (VIN), J1.7, J2.1, J3.7, J4.1, J5.1, U1.5 (VCC), U2.4 (OUT+)

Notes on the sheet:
2x BTS7960 Breakout
2x Potentiometer Feedback

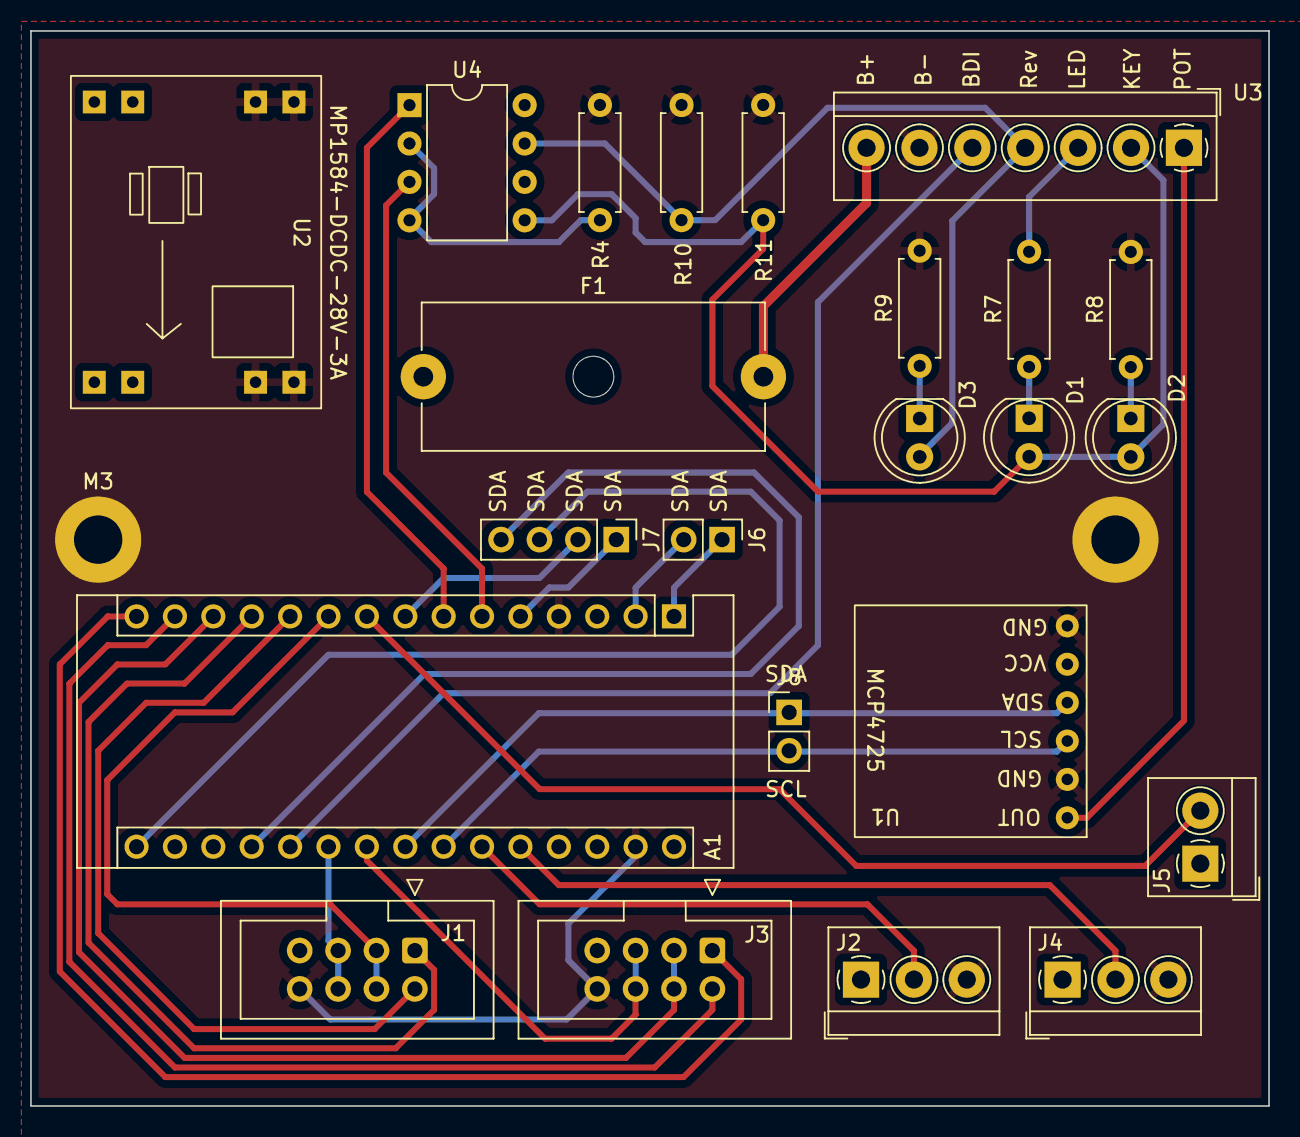
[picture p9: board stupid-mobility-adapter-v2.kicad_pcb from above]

Board: 2 copper layers, 81.9 x 71.1 mm, 24 parts (0 on the bottom side), 34 nets.

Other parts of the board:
M3: MountingHole_3.2mm_M3_ISO7380_Pad

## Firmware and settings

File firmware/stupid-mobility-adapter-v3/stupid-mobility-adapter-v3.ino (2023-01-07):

#include "comms.h"
#include "network.h"
#include "ps3.h"
//#include "rcinput.h"
#include "config.h"
//#include "dc_motor.h"
#include "curtis.h"
#include "actuator.h"
#include "safety.h"
#include <Arduino.h> // Necessary to make vscode problem free. vscode 1.50.1 bug workaround.

// bastard thing wont fit onto a stock esp32 uses 1459006 bytes (111%) Max size is 1310720
// You have to use a non-standard partitioning scheme for the esp32. Doubtful that the new version will fit on a nano either.

void setup() {
  startSafety();
  startComms();
  startNetwork();
  setupPs3();
  setupActuator();
  //setupMobility();
  setupCurtis(); 
  //startRCInput();
  Serial.println("[INFO] Setup Completed");
}

void loop() {
  doSafety();
  doNetworking(); 
  checkPs3();
  //checkConnection();      // comms.cpp - Only needed when relying on the serial connection for safety critical control
  checkSerialComs();      // comms.cpp - Needed if recieving serial data for control. So, not yet.
  if (error) {
    stopActuators();
    doCurtisControl();
    //stopMotor();          // for use with pwm motor driver.
  }
  else {
    doActuatorControl();
    doCurtisControl();
    //doMobilityControl();  // for use with a pwm motor driver
  }
}

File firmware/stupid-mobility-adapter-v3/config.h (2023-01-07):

/*
 * NOTES
 * 
 * When flashing the microcontroller, make sure that the main battery power is disconnected and the ESTOP is pushed

*/

#ifndef CONFIG_H
#define CONFIG_H
#include <Arduino.h>

// variables that lots of things want to access anyway
extern int motorSpeed;
extern int actuatorSetpoint_request;
extern int toolSetpoint_request;

#define errorPin 36
#define BATT_DIV_PIN 35 // 15 can't be used while BT and Wifi are enabled... https://docs.espressif.com/projects/esp-idf/en/release-v4.0/api-reference/peripherals/adc.html

// Steering Actuator
// For actuator, extend is....
#define ACT_EN 27       // BTS1_EN
#define ACT_R_PWM 14    // BTS1_RPWM
#define ACT_L_PWM 12    // BTS1_LPWM
#define ACT_FB 34       // ACT1_FB

#define ACT_P 2
#define ACT_I 0.1
#define ACT_D 0

#define actCentre 1850              // 500 on 0-1024 scale (sctbot 889)
#define actMax 900
#define actMin 2800 //1000
#define actDeadband 10              //Stops the actuator hunting quite so much

// Tool Actuator
// For actuator, extend is....
// voltages:positions are steering(vin:4.75v, centre:2.48v, right:1.34v, left:3.5v)
//                            tool(vin:4.75v, max:1.9v, min 0.4v)

#define TOOL_EN 32      // BTS0_EN
#define TOOL_R_PWM 33   // BTS0_RPWM
#define TOOL_L_PWM 25   // BTS0_LPWM
#define TOOL_FB 39      // ACT0_FB

#define TOOL_P 2
#define TOOL_I 0.1
#define TOOL_D 0

#define toolMin 10
#define toolMax 1750
#define toolCentre floor(abs(toolMax - toolMin)/2); //  0-1024 scale
#define toolDeadband 7              //Stops the actuator hunting quite so much
#define toolStep 10

// Communication 

// Wifi configuration
//#define WIFI_TYPE 1  //Station mode . be sure you have network access configured if using this mode. Otherwise you'll have an infinite while loop on your hands before youve finished the setup loop
#define WIFI_TYPE 2  //Access Point mode. For ease of use on demo day. Remember to configure your desired wifi credentials below
//#define WIFI_TYPE 3  //Station + Acccess mode // DONT DO THIS YET

// Serial control input
#define MESSAGELENGTH 4
#define BAUDRATE 115200
#define COMCHECKTIME 250

// Servo Input pins
#define SERVO_IN_THROTTLE_PIN 16
#define SERVO_IN_STEER_PIN 17

// Select general configuration below
// #define NANO               // AVR microcontroller connecter to two BTS7960 motor drivers. Probably wont work right now. see https://github.com/rwlloyd/Scooterbot for more. 
// #define ALL_BTS7960        // ESP32 microcontroller dual bts7960. 
#define CURTIS                // esp32 microcontroller curtis unit bts7960 actuator

#ifdef NANO
/*
 * Pinout configuration for Arduino nano controlling two IBT_2 Motor drivers for actuator 
 * and speed control, relay board for. probably might work.
*/
  // for Brake
  #define BRAKE_PIN 11
  #define errorPin 2
  // for motor, left is backwards
  #define MOT_R_EN 3
  #define MOT_L_EN 4
  #define MOT_L_PWM 6
  #define MOT_R_PWM 5
  #define MOT_L_IS A1
  #define MOT_R_IS A2
  #define motorCentre 128
  #define motorMin 50
  #define motorMax 255
  #define speedLimit 128
  // For actuator, extend is....
  #define ACT_R_EN 7
  #define ACT_L_EN 8
  #define ACT_R_PWM 9
  #define ACT_L_PWM 10
  #define ACT_FB A0
#endif

#ifdef ALL_BTS7960
/*
 * For ESP32 pinout with dual IBT_2 on v3 board 
 * BTS0 is the motor connection BTS1 is the Actuator. 
 * ACT1_FB is used for actuator controld to make adding a curtis unit to the mix simpler.
*/
// for Brake
#define BRAKE_PIN 13
// for motor, left is backwards
#define MOT_EN 32 // pins are now tied together
#define MOT_L_PWM 25
#define MOT_R_PWM 33
//#define MOT_IS 35
#define motorMin 50
#define motorMax 255
#define speedLimit 255
#endif

#ifdef CURTIS
/*
 * For ESP32 with curtis unit and IBT_2 actuator FB as ALL_BTS7960
*/
#define dirPin 19
#define enablePin 18
#define MCP4725_I2C_ADDR 0x60  // or 0x62 or 0x63
#define CURTIS_DEADBAND 5
#endif

#endif

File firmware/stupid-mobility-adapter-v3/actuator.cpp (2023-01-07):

/*
   To Do

   Need a way to adjust the centre point of the steering. While we're at it, Min and Max too

*/

#include <Arduino.h>
//#include <analogWrite.h>
#include <movingAvg.h>
#include <PID_v1.h>
#include "comms.h"
#include "safety.h"
#include "config.h"
#include "ps3.h"

// Steering Actuator Variables
int actPosition;
int actuatorSetpoint_request = 0;
movingAvg actPositionAvg(4);                // define the moving average object

int Max = actCentre - (90 * 4);
int Min = actCentre + (90 * 4);
int vel = 200;

//Define Variables we'll be connecting to
//double actuatorSetpoint, actuatorInput, actuatorOutputLeft, actuatorOutputRight;
double actSetpoint, actInput, actOutput;

//Specify the links and initial tuning parameters
double Kp = ACT_P, Ki = ACT_I, Kd = ACT_D;
PID motorPID(&actInput, &actOutput, &actSetpoint, Kp, Ki, Kd, DIRECT);

// Tool Actuator Variables
int toolPosition;
int toolSetpoint_request = 0;
movingAvg toolPositionAvg(4);                // define the moving average object

// int toolMax = toolCentre - (90 * 4);
// int toolMin = toolCentre + (90 * 4);
int toolvel = 200;

//Define Variables we'll be connecting to
//double actuatorSetpoint, actuatorInput, actuatorOutputLeft, actuatorOutputRight;
double toolSetpoint, toolInput, toolOutput;

//Specify the links and initial tuning parameters
double Kpt = ACT_P, Kit = ACT_I, Kdt = ACT_D;
PID toolPID(&toolInput, &toolOutput, &toolSetpoint, Kpt, Kit, Kdt, DIRECT);

void stopActuators() {
  // Steering Actuator 
  analogWrite(ACT_R_PWM, 0);
  analogWrite(ACT_L_PWM, 0);
  // Tool Actuator
  analogWrite(TOOL_R_PWM, 0);
  analogWrite(TOOL_L_PWM, 0);
}

void setupActuator() {
  pinMode(ACT_FB, INPUT);
  pinMode(ACT_EN, OUTPUT);
  pinMode(ACT_R_PWM, OUTPUT);
  pinMode(ACT_L_PWM, OUTPUT);

  pinMode(TOOL_FB, INPUT);
  pinMode(TOOL_EN, OUTPUT);
  pinMode(TOOL_R_PWM, OUTPUT);
  pinMode(TOOL_L_PWM, OUTPUT);

  // Read the actuator position
  actInput = analogRead(ACT_FB);
  toolInput = analogRead(TOOL_FB);
  // begine the position averaging.
  actPositionAvg.begin();
  toolPositionAvg.begin();
  // set the inital setpoint to the centre position
  actSetpoint = actCentre;
  toolSetpoint_request = 1750; // toolMax; bad idea to make the tool move by default at startup
  // Just to be on the safe side, make sur the actuator is disabled
  // stopActuator(); /// dont request a position then turn everything off....
  digitalWrite(ACT_EN, LOW);
  digitalWrite(TOOL_EN, LOW);
  //turn the PID on
  motorPID.SetMode(AUTOMATIC);
  motorPID.SetOutputLimits(-255, 255); // default is 0-255

  toolPID.SetMode(AUTOMATIC);
  toolPID.SetOutputLimits(-255, 255); // default is 0-255
}

void doActuatorControl() {
  motorPID.Compute();
  toolPID.Compute();
  if (!enable) {
    stopActuators();
    digitalWrite(ACT_EN, LOW);
    digitalWrite(TOOL_EN, LOW);
  }
  else {
    digitalWrite(ACT_EN, HIGH);
    digitalWrite(TOOL_EN, HIGH);
    actSetpoint = map(actuatorSetpoint_request, -128, 128, actMin, actMax);
    toolSetpoint = constrain(toolSetpoint_request, toolMin, toolMax); //// Not really happy with this. needs better control
    // toolSetpoint = map(toolSetpoint_request, -128, 128, toolMin, toolMax);
    //Serial.println(Setpoint);
    actPosition = analogRead(ACT_FB);
    toolPosition = analogRead(TOOL_FB);
    actInput = actPositionAvg.reading(actPosition);
    toolInput = toolPositionAvg.reading(toolPosition);
    if (debugActuator) {
      Serial.print(actSetpoint);
      Serial.print(", ");
      Serial.print(actPosition);
      Serial.print(", ");
      Serial.print(actInput);
      Serial.print(", ");
      Serial.print(actOutput);
      Serial.print(", ");
      Serial.print(toolSetpoint);
      Serial.print(", ");
      Serial.print(toolPosition);
      Serial.print(", ");
      Serial.print(toolInput);
      Serial.print(", ");
      Serial.println(toolOutput);
    }

    // Set PWM for Steering
    if (actInput <= actSetpoint + actDeadband && actInput >= actSetpoint - actDeadband) {
      analogWrite(ACT_R_PWM, 0);
      analogWrite(ACT_L_PWM, 0);
    }
    else if (actInput > actSetpoint + actDeadband) {
      digitalWrite(ACT_EN, HIGH);
      analogWrite(ACT_R_PWM, int(abs(actOutput)));
      analogWrite(ACT_L_PWM, 0);
    }
    else if (actInput < actSetpoint - actDeadband) {
      // FOR this setup, left turn is extending the actuator to turn ...
      digitalWrite(ACT_EN, HIGH);
      analogWrite(ACT_L_PWM, int(abs(actOutput)));
      analogWrite(ACT_R_PWM, 0);
    }

    // Set PWM for Tool
    if (toolInput <= toolSetpoint + toolDeadband && toolInput >= toolSetpoint - toolDeadband) {
      analogWrite(TOOL_R_PWM, 0);
      analogWrite(TOOL_L_PWM, 0);
    }
    else if (toolInput > toolSetpoint + toolDeadband) {
      digitalWrite(TOOL_EN, HIGH);
      analogWrite(TOOL_R_PWM, int(abs(toolOutput)));
      analogWrite(TOOL_L_PWM, 0);
    }
    else if (toolInput < toolSetpoint - toolDeadband) {
      // FOR this setup, left turn is extending the actuator to turn ...
      digitalWrite(TOOL_EN, HIGH);
      analogWrite(TOOL_L_PWM, int(abs(toolOutput)));
      analogWrite(TOOL_R_PWM, 0);
      // Serial.println(toolOutput);

    }
  }
}

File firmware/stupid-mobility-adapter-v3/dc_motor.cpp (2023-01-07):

#include <Arduino.h>
#include <BTS7960.h>
//#include <analogWrite.h>
#include <movingAvg.h>                  // https://github.com/JChristensen/movingAvg
#include "safety.h"
#include "config.h"
#include "comms.h"
#include "ps3.h"

#if (NANO || ALL_BTS7960)
BTS7960 motorController(MOT_EN, MOT_EN, MOT_L_PWM, MOT_R_PWM);

int lastMotorSpeed;
int motorDesired;

movingAvg motorDesiredAvg(10);                // define the moving average object

void setupMobility(){
  //Brake Pin
  pinMode(BRAKE_PIN, OUTPUT);
  pinMode(MOT_EN, OUTPUT);
  pinMode(MOT_L_PWM, OUTPUT);
  pinMode(MOT_R_PWM, OUTPUT);

  motorDesiredAvg.begin();
  motorController.Stop();
  motorController.Disable();
}

void stopMotor(){
    digitalWrite(BRAKE_PIN, enable);
    motorController.Stop();
    motorController.Disable();
}

void doMobilityControl(){
    if (!enable) {
        stopMotor();
    }
    else {
        digitalWrite(BRAKE_PIN, enable);
        motorController.Enable();
        
        motorDesired = motorDesiredAvg.reading(motorSpeed);
        if (motorDesired == 0) {
            motorController.Stop();
        }
        if (motorDesired < 0) {
            motorController.Enable();
            motorController.TurnRight(map(motorSpeed, 128, 0, motorMin, speedLimit));
        }
        if (motorDesired > 0) {
            motorController.Enable();
            motorController.TurnLeft(map(motorSpeed, -128, 0, motorMin, speedLimit));
        }
    }
}

#endif

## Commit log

2022-03-04 Initial Commit - Kicad Files Mainly
    [stupid-mobility-adapter-v2.kicad_pcb, stupid-mobility-adapter-v2.kicad_sch]
2022-04-19 Hardware Prototype Working. Code basic function.
    [stupid-mobility-adapter-v3.kicad_pcb, stupid-mobility-adapter-v3.kicad_sch]
2022-04-23 Updated readme. added servo debug switch
2022-04-23 Added buzzer and servo input to v3 pcb
    [stupid-mobility-adapter-v3.kicad_pcb, stupid-mobility-adapter-v3.kicad_sch]
2022-05-23 Commit before doing first fork for new project
    [stupid-mobility-adapter-v3.kicad_pcb]
2022-05-23 Added tool to actuator.cpp etc for testing
2022-05-24 Tested on hardware. Changed actuator limits and changed drive direction. Broke networking.
    [actuator.cpp, config.h, curtis.cpp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]
2022-07-25 updated kicad files
2022-10-13 config serial ctl, change esp32
2023-01-07 build and setup board for v4.1/4.1
    [stupid-mobility-adapter-v3-B_Cu.gbr, stupid-mobility-adapter-v3-B_Mask.gbr, stupid-mobility-adapter-v3-B_Silkscreen.gbr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]
